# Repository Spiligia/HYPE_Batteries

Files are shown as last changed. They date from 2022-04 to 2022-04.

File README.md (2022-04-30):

**Boston University EC 463 & 464 Senior Design Project**

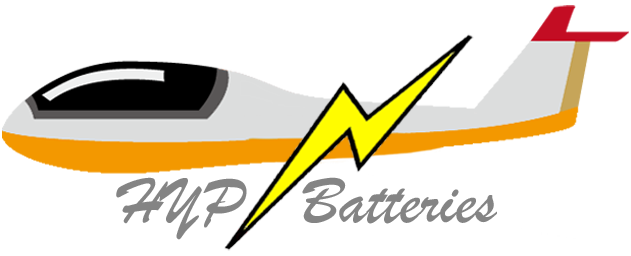
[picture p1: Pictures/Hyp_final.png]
HYP Logo


Members: Spencer Piligian, Ismaeel AlAlawi, Steven Wang, Yusheng Chen and Daniel Kao

## Welcome to Team 23: HYP Batteries! 

Our hybrid-chemistry battery pack design aims to fill niche market gap in high performance battery pack for small aircraft by combining two batteries with two different discharge characteristics. These two cell chemistries can achieve a variable-max discharge rate, allowing us to design a smaller battery pack while also fulfilling power requirements during the launch. This pack setup will help eGliders achieve a safe flight through the use of electric power and as a result, will minimize the risk of mechanical failure for our client’s conventional mechanical engines, whose vibration causes other parts of the aircraft to wear out and ultimately increases the chance of failure.

Link to google drive for more information / process development 

https://drive.google.com/drive/u/0/folders/0AN8LmBJzQ7HJUk9PVA

For member access please email: spiligia@bu.edu

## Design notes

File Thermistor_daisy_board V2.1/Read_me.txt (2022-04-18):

To run these files you will need the latest version of Kicad PCB design software (6.0.x). 
It is free and easily downloadable from https://www.kicad.org/

to open the schematic you will open the temp_proto_v2.1 (KiCad Project 6.0)
to open the pcb file you will open the temp_proto_v2.1 (KiCad Board)

to order a pcb you can either

1. zip this folder and morder from JLCpcb (all 'cam' files in this folder are made w/ respect to jlc's parameters)
2. find the setting in kicad and create new gerbers

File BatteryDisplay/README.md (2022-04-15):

# Battery Display #

App build using Qt Creator

Based on HeatRateGame as a template to check for bluetooth & BLE connection, connect
to devices, discover services and connect to the device to receive BLE data.

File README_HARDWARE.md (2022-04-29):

## Contents
- [Overview](#overview)
- [Battery Temperature Display](#Testbench-Hardware-Setup)
- [Lists of the Hardware Components](#Lists-of-the-Hardware-Components)
- [Setup-Procedure](#Setup-Procedure)
- [3D-Model-Battery-Holders](#3D-Model-Battery-Holders)
- [Ideal Diode](#Ideal-Diode)
- [Temperature-sensing-module](#Temperature-sensing-module)
- [Bill-of-Materials](#Bill-of-Materials)

## Overview

Our project HYP Batteries has several hardware components. These components include designs for a testbench which can handle upto 15A of continuous current, a temperature monitoring circuit schematic for use with a microcontroller, and an Ideal Diode controller for minimization of losses. 

## Testbench-Hardware-Setup

In order to properly conduct this testbench setup, there are several hardware need to be met. On the hardware side, the battery circuit includes a 9V DC power supply that is connected to a 30A relay and that relay is connected to a parallel connection of LiFePO4 and Li-ion batteries in a 3:2 ratio respectively, in which a Schottky barrier diode is placed in series with the Li-ion batteries to prevent reverse leakage current from the LiFePO4 cells to the Li-ion cells.  It is important to note that this Schottky barrier is part of a diode bridge rectifier (i.e. terminals are adjusted accordingly in order to retrieve a single Schottky barrier diode from the rectifier circuit). There exists a 40A fuse that is connected in series with the motor controller and the current sensor for safety standard purposes. In the event of a full short we would expect a current spike up to 550A – ~9.9V/18mΩ (internal resistance) – causing the fuse to blow nearly instantly.  The motor controller is properly connected to an inductor using connection shells and the inductor is then coupled with two power resistors in order to dump energy – by connecting the inductor in series with the power resistor, the current can be tuned easily through the motor controller. For safety reasons, we will be using a thermocouple that will log the temperature of the batteries; the digital thermocouple of the motor controller will log the temperature of the MOSFETs in the motor controller. The battery and motor controller voltages will also be recorded appropriately using multimeters. 

## Lists-of-the-Hardware-Components:
- 3 x LithiumWerks A123 P6 (3.3V, 2500 mAh) lithium iron phosphate (LiFePO4) rechargeable battery cells 
- 2 x Molicel P42A (3.6V, 4200 mAh) lithium-ion (Li-ion) rechargeable battery cells 
- 3 x BeilaMoo 26650 3.7V single slot battery holders
- Surface mount technology (SMT) KeyStone Electronics 21700/20700 dual battery holder w/ coil springs
- IXYS VUO 190-08 NO7 three-phase diode bridge rectifier
- 2 x 1.5kW 1Ω resistors 
- 40A automotive fuse  
- TE Connectivity Potter & Brumfield T9GS1L14-12 30A relay 
- TeamTriforceUK A50S V2.1 (50A burst) VESC-supported motor controller
- XT30 connector (battery input) 
- MR30 connector and cable cover (motor output) 
- 2 x pico-clasp connector shells
- microUSB to USB cable
- 10 µH inductor
- Male-to-male jumper wires
- Test Products Intl. (TPI) dual temperature thermocouple digital thermometer 343
- 1 x 10kΩ resistor
- Alligator clips 
- Crocodile clips
- Hook clips
- Banana plugs
- Electrical ring tongue terminals AWG 18-22
- 2 x TE Connectivity TE2500B1R0J 50 W - 2500 W chassis-mount power resistor 
- AWG 8, 12 & 18 wires
- ACDelco SuperALKALINE 6LR61 9V battery
- PKCELL Extra heavy duty 6F22 9V battery
- 2 x battery snap connectors (9V) 
- Electrical insulation tape and masking tape
- 2 x Multimeter

## Setup-Procedure
- Battery testbench hardware side (see Figure 1 for visual reference)
    - Attach 9V connector battery to the relay (top left and right connections) by soldering battery snap connectors to energize the relay’s coil
    - Place each of the three LiFePO4 batteries in their respective single slot battery holders
    - Place both Li-ion batteries in the dual slot battery holder
    - Solder the wires connecting the LiFePO4 battery holder contacts in series and solder the first ring terminal wire to one of the LiFePO4 battery holders accordingly and the other to the Li-ion dual battery holder to create the parallel connection
    - Connect the ring terminal connected to the LiFePO4 battery holders into terminal ~C (phase-C) of the rectifier and the other terminal (which is connected to Li-ion batteries) to terminal B- (see Figure 2 for rectifier reference schematic) 
    - Solder the LiFePO4 battery holder and rectifier junction into the 30A relay’s bottom right terminal 
    - Solder the 40A fuse into the bottom-right terminal of the Li-ion battery holder and connect its other end to the negative top terminal of the current sensor 
    - Connect the positive top terminal of the current sensor to the motor controller positive XT30 connection; the negative terminal of this connection should be connected to the multimeter accordingly for voltage readings.
    - Connect the positive terminal of the motor controller MR30 connector into the positive terminal of the multimeter to complete the connection for motor controller voltage readings
    - Connect the A50S motor controller to the laptop using micoUSB-USB cable  
    - Connect the positive and negative terminals of the motor controller-motor junction to the positive and negative terminals of the power resistor respectively 
    - The test bench setup should look similar to Figure 3

 - Diode, 9V batteries, and properly soldered electrical connection testing (if necessary)
    - Using a multimeter, test the voltages/currents across the terminals of the Schottky junction diode and the 9V batteries, as well as other electrical connections in the circuit to ensure that the connections aren’t faulty, i.e. improperly soldered or connected.

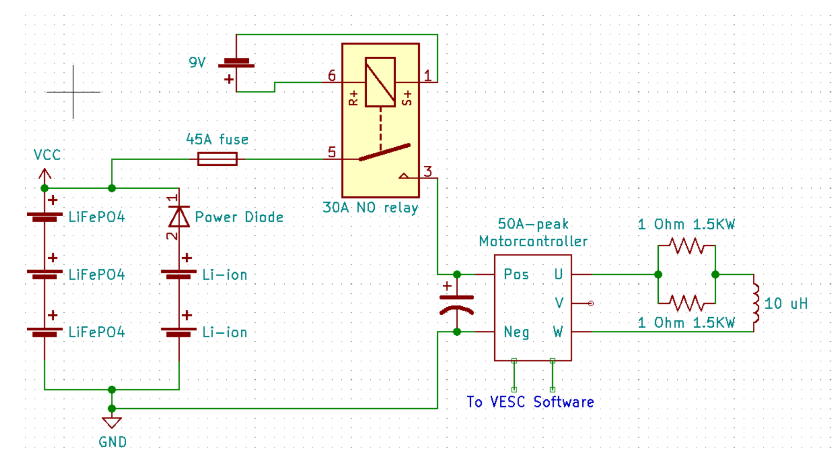
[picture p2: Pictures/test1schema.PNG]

Figure 1: KiCad EDA design schematic of In-lab test 1 (manual current scheduling). Schematic in terms of motor controller design. 

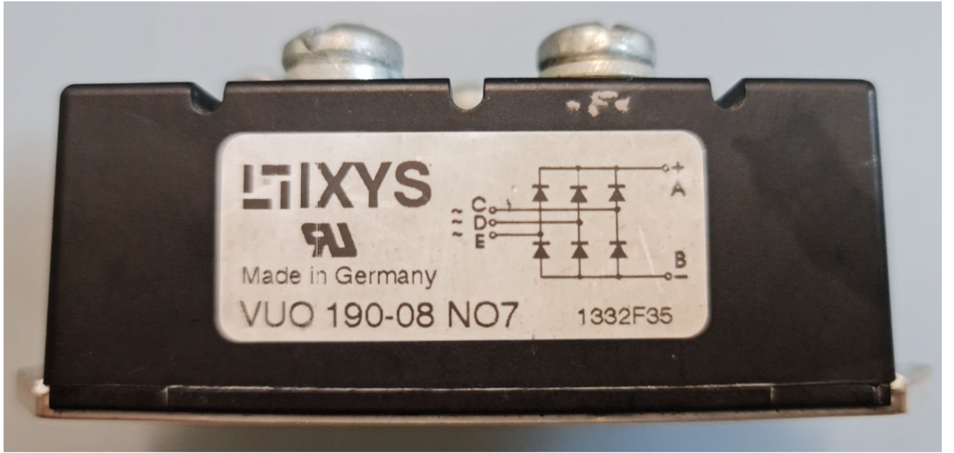
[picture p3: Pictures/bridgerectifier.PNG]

Figure 2: Reference schematic of three-phase diode bridge rectifier. Terminals ~C and B- are used to retrieve a single Schottky barrier from the rectifier. 

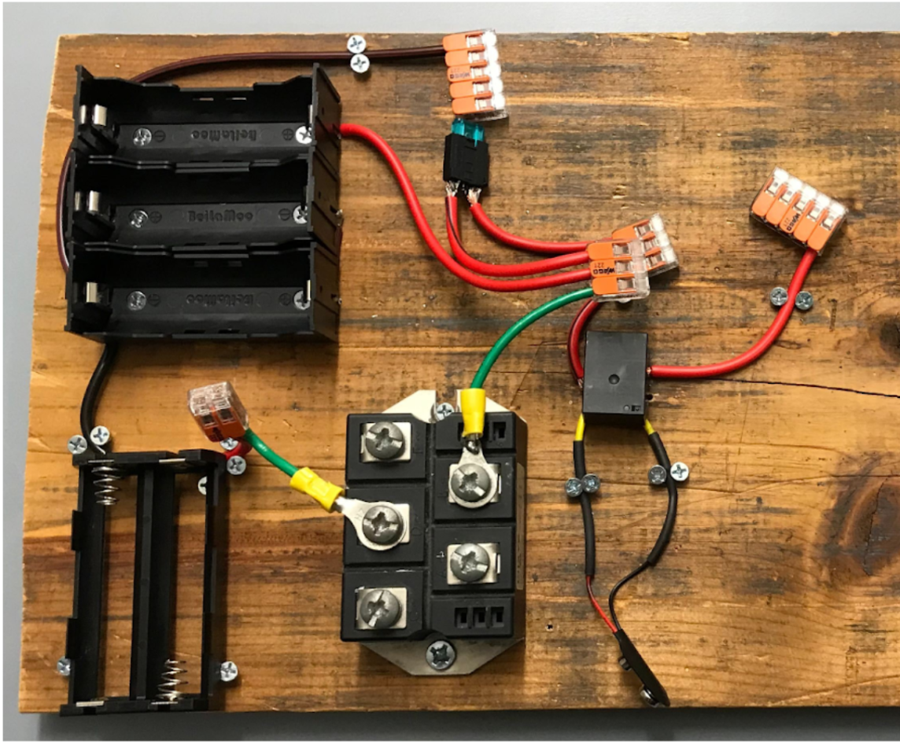
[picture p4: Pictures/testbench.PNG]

Figure 3: Battery testbench reference 

For the future testing,the additional batteries will be added to the testbench when you want to scale up. In additional, you will required to change the fuse and also the wire, since those component are not capable of handling higher current and high voltage. 

## 3D-Model-Battery-Holders
Base on our testing, we found that the battery holder that we bought online are no capable of handling high heat, so we decided to 3D model the battery holders by using pla material. The holder for the LiFePO4 contains the base and the top.(Figure 4&5) For Lithium-ion, it will need two identical 3d models to hold battery in place.(Figure 6) Since our final design pack is 19 series 1 parallel of LiFePO4 and 12 series 8 parallel of Lithium-ion, we will need two sets of LiFePO4 battery holders and 4 sets of Lithium-ion battery holders.  

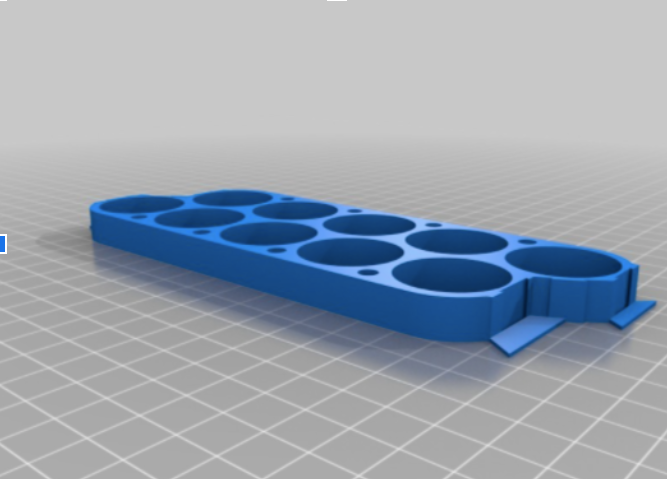
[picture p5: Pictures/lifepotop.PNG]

Figure 4:LiFePO4 Battery Holder Top 26650

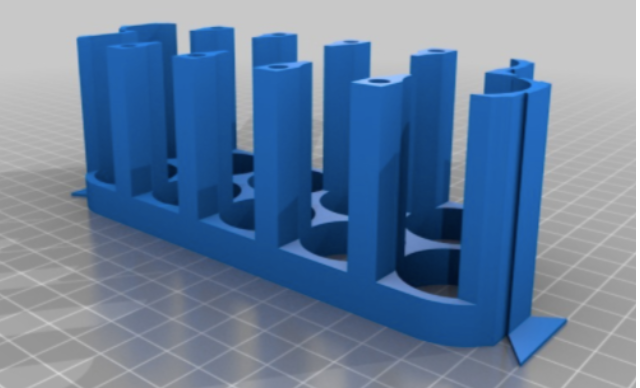
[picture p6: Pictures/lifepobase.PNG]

Figure 5:LiFePO4 Battery Holder Base 26650

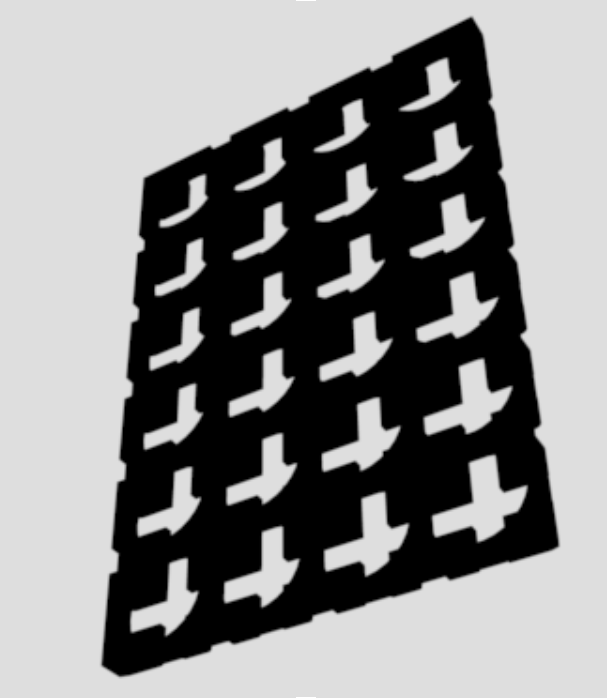
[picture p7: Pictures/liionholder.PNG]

Figure 6:Lithium-Ion Battery Holder 21700

## Ideal-Diode
 
The ideal diode controller will replace the schottky diode for the full scale battery pack. This ideal diode is used to reduce the voltage drop across the diode when the current reaches higher magnitudes. There are two main parts to this component, the ideal diode controller itself and the PCB to house the components. In the PCB, we use two MOSFETs (parts listed in schematic) to distribute the current evenly. To deal with the problem of heat dissipation on the board, we have multiple solutions. The board will have two copper pours on both the top and bottom layers as well as a heat sink on top to further distribute the heat. Additionally, the configuration of the MOSFETs and trace width are also very important for distributing heat. Copper busbars must be soldered on the traces for the 300A current path to help handle the current. More details can be found in the schematics and board diagrams below. 

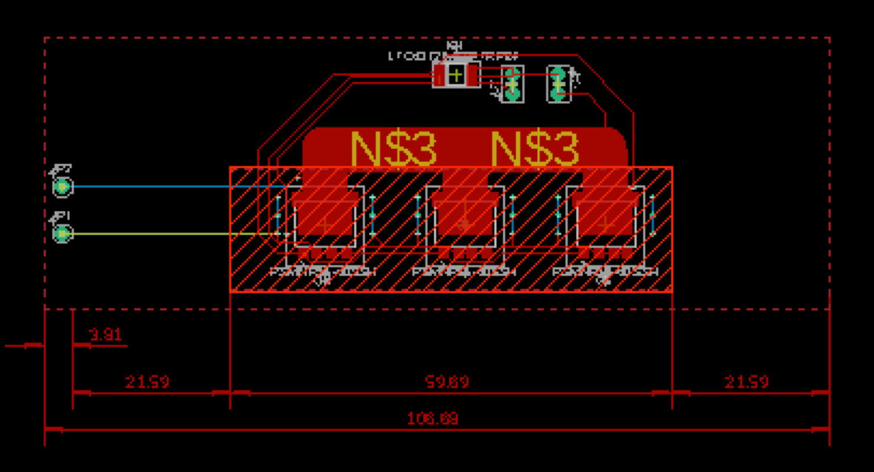
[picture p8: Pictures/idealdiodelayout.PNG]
ideal diode boadr


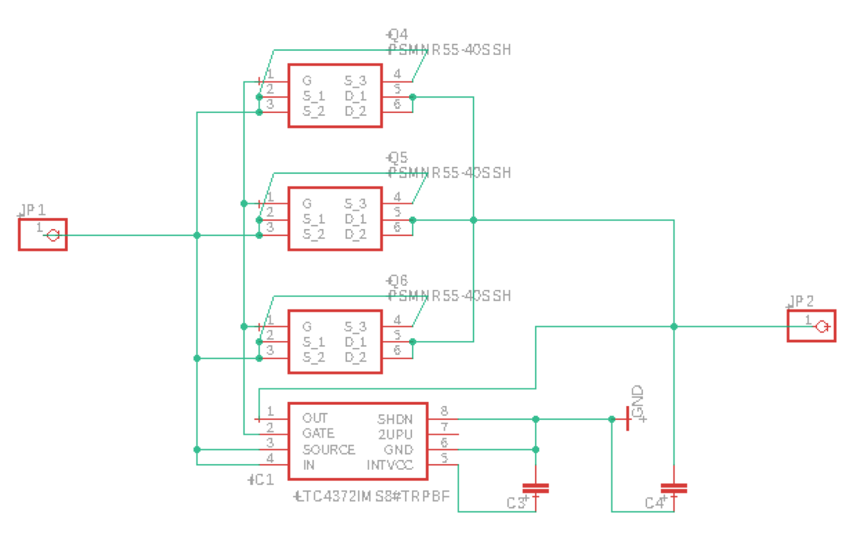
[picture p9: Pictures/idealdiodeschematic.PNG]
idealdiodeschema


## Temperature-sensing-module
The temperature sensing module circuit is based on the use of thermistors in a higher temperature application. Any 10k thermistors will do as long as special care is taken to tuning and programming of the microcontrollers ADC pin and readings. Special care will also need to be taken into account for the speed of the system, specifically rise and fall time. With a 0.1uF capacitor acting as the low pass filter into the final op amp the frequency is limited by the rise time of the capacitor. This can be measured through software simulations or mathematical circuit analysis. To manufacture the PCBs you will need to use KiCAD — a free pcb design software— to get the necessary files to order the PCBs. To set up the modules they will need to be daisy chained in accordance with the circuit diagram to ensure proper orders of signals and functions. A Premade gerber folder is available in Github for the ordering of the boards.

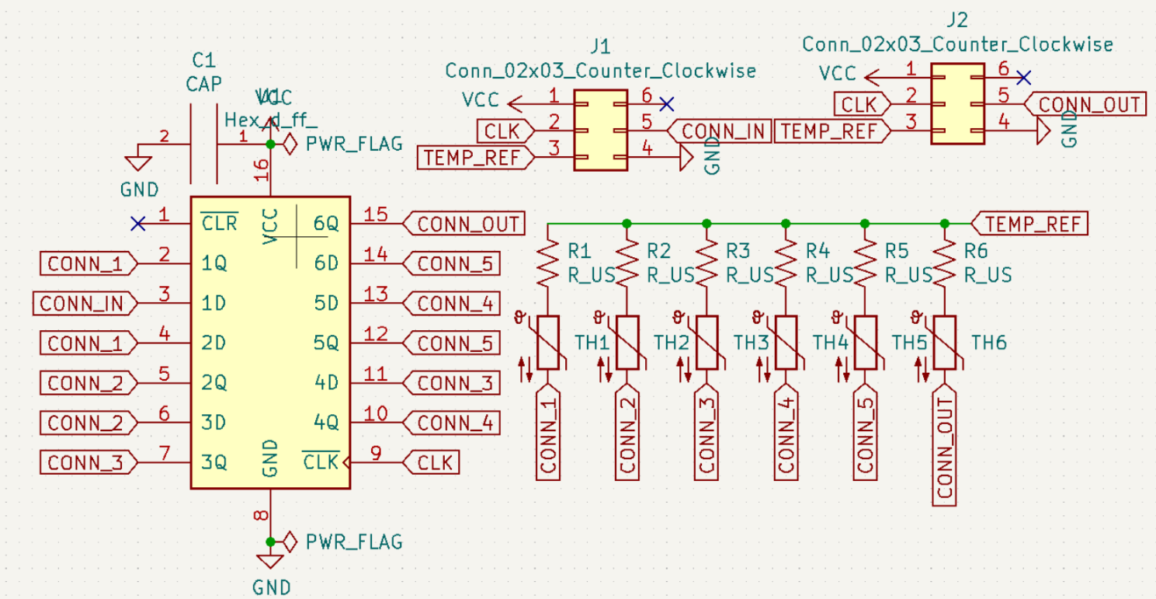
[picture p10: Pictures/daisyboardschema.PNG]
daisyboard1


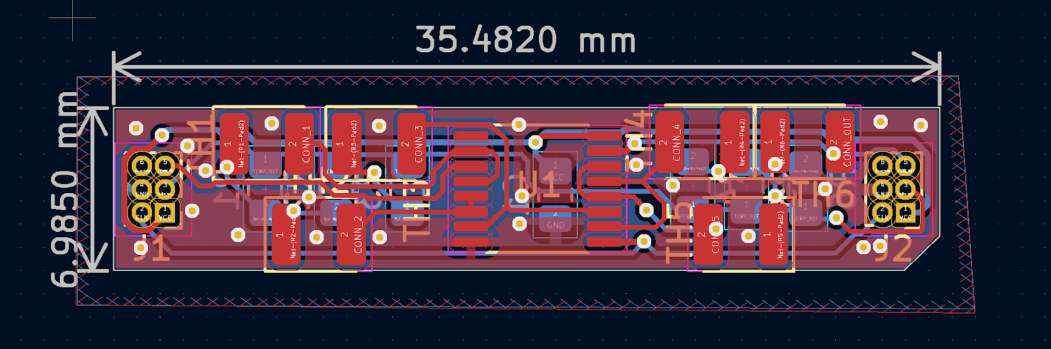
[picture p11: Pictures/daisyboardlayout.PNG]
daisyboard2


## Bill-of-Materials

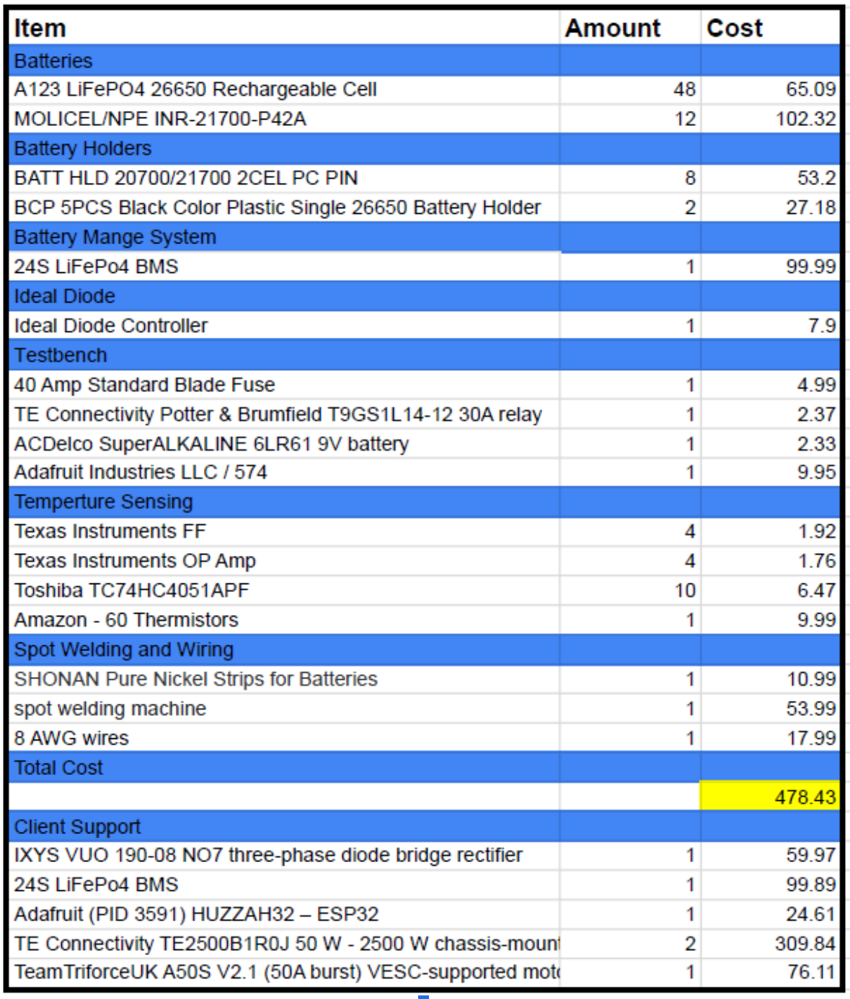
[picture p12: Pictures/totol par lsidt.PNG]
bom


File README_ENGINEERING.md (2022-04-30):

To quick start this project first read throught the software and hardware README reports. The project can be split into three sections: Battery, Hardware and Software

## Battery-Pack
If you like to come up with your own configuration of the battery pack, you can use the simulation code provide in the Simulation_Code_and_Result folder. The spec sheet of different batteries are in the folder called Battery_Pack_Design, this will help you to create csv file for the simulation code. The process of creating csv file are listed in the software README_SOFTWARE.md. You would be able to come up different graphs and charts showing details such as power, discharge rate, voltage and etc. 

## Hardware 
One may want to test on the pre designed testbech and the schematic provided in the hardware README will allow for easy hardware setup. The README_HARDWARE.md provide the process of the testing and also the materials been used for testing. 

To start this project one would want to produce and test the ideal diode design and the temperature sensing module. The next step is to take the information gained from that and iterate the designs. Then combine the temperature sensor data with the battery temp viewer to finalize the system for the client. 

If someone want to looks at past prototype results and also self test results and it is in the folder called Prototype_Test and Self_Test. 

It is possible to increase the voltage and currents to the full battery size and then design mechanical components to ensure isolation from the cabin and safety from factors like vibration and drops. Since our model is just an small scale model of the whole pack, scaling up the battery pack may increase the safety concern.

## Software

If changes and revision need to be done to the simulation or battery display see README_SOFTWARE.md for more information regarding setting up the proper simulation tools and source code for the project.

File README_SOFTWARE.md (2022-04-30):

Team #23 Software Report

## Contents
- [Overview](#overview)
- [Battery Temperature Display](#Battery-Temperature-Display)
- [Qt Creator Download Instruction](#Qt-Creator-Download-Instructions)
- [Qt Creator Interface](#Qt-Creator-Interface)
- [Instruction to run Battery Display App](#Instruction-to-run-Battery-Display-Application)
- [Battery Temperature Simulation App](#Battery-Temperature-App)
- [Battery Pack Configuration Simulation](#Battery-Pack-Configuration-Simulation)
- [Battery Pack “Naive” Testbench Automation](#Battery-Pack-“Naive”-Testbench-Automation)
- [Battery Pack Structural Testbench Automation](#Battery-Pack-Structural-Testbench-Automation)

## Overview

Our project HYP Batteries has three software operations required to test our hardware: battery pack simulation, battery pack temperature monitoring, and battery pack automated testing. 

## Battery-Temperature-Display

The preferred integrated development environment (IDE) for battery temperature display is Qt Creator which is a cross platform for C++, javascript and QML. The software is available to download online through Qt Creator website, https://www.qt.io/.

## Qt-Creator-Download-Instructions

1. Users must click on the download button below the website
2. Direct to “Downloads for open source users” to get a free copy
3. After navigating to that page the user will need to scroll all the way down 
4. Then hit the download button and follow along with the instructions. You might need to download additional features like Xcode & Xcode command line tools for Mac OS
5. Select an installation folder on your device and check off custom installation
6. Under custom installation page select Qt 6.3.0 default feature which will selection all options within the folder
7. Afterward read Terms of Service page and begin downloading process for Qt Creator

## Qt-Creator-Interface

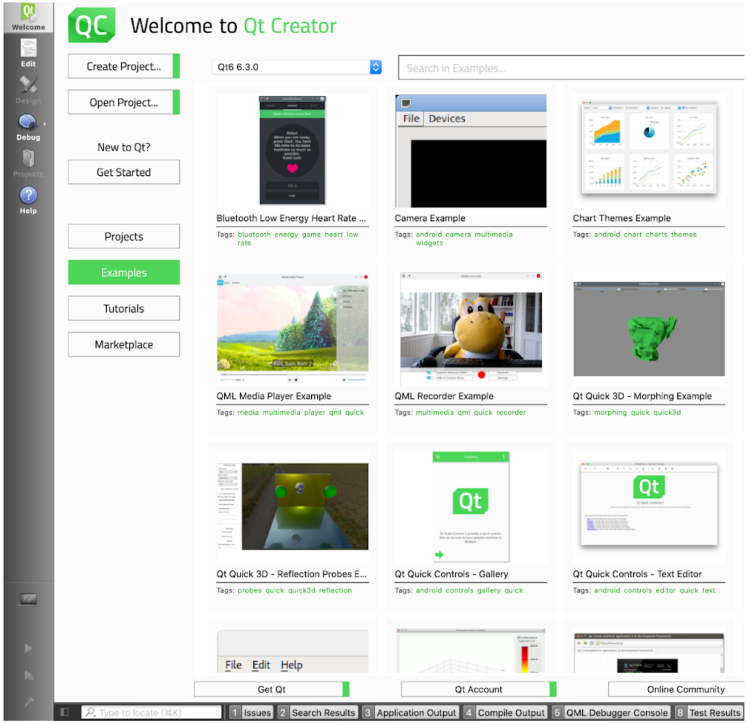
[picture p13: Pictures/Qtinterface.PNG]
qt interface pic


Basic rundown of Qt creator interface, welcome tab is where you can find example templates, create and open projects, the edit tab will be the project you're working on after you select a file on the welcome tab, the computer icon is how you wish to emulate the app, there’s two play button one to run the file and other is to debug, lastly the hammer icon is to compile the files prior to running.

## Instruction-to-run-Battery-Display-Application

After downloading Qt Creator navigate to github to download the source code for battery temperature display app: https://github.com/Spiligia/HYPE_Batteries/tree/main/BatteryDisplay. From there launch the Qt Creator application and open the project, make sure you select the Battery Display folder. Navigate to the Measure.qml file to adjust the amount of battery cells you desire in series and parallel. From there you can choose to emulate the application on the PC or another platform either Android or Apple. You must have additional packages downloaded to run on either Android and Apple platform that Qt Creator would recommend to download prior to building the files.  

## Battery-Temperature-App 

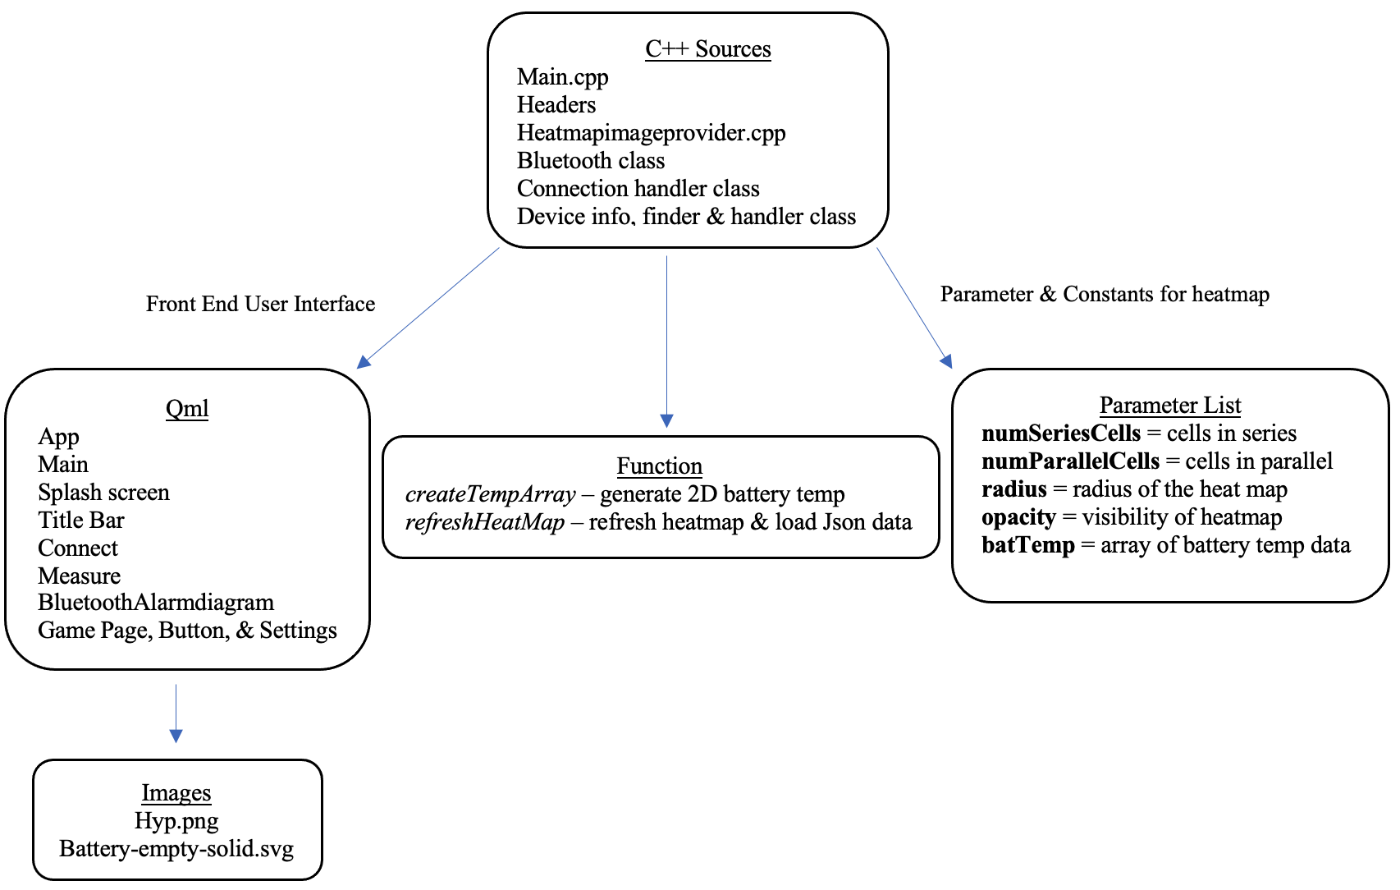
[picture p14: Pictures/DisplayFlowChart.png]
Display FlowChart


The battery temperature display used Qt Example: Bluetooth Low Energy Heart Game as a template for its design that can be found under the Examples tab on Qt Creator. The C++ Sources are mainly untouched except for Heatmapimageprovider.cpp, this was sourced from our client. The following QML files were modified to accommodate the app design: SplashScreen.qml, TitleBar.qml and Measure.qml. Below are relevant documentations done to the user interface in the qml files and the cpp file: 

- SplashScreen.qml: added logo image for the app
- TitleBar.qml: changed the page indicator size & text on the app title navigation bar
- Measure.qml: comment out unused code from the heart rate game, added heatmap image & integrate parameters required for it to function from Heatmapimageprovider.cpp, added command to display & remove heatmap temperature data on UI & User console, function to generate random heatmap data temperature and reload heatmap button
- Heatmapimageprovider.cpp: added new Json Array object batTemp to grab random generate temperature data and attempt to write onto the actual heatmap on the UI
	
## Battery-Pack-Configuration-Simulation

In order to do the simulation, a notebook environment that can write and read Julia script is needed. After obtaining a coding environment like Jupyter notebook, the next steps are to obtain battery data specification sheets for the batteries you wish to simulate. These specification sheets must include: cell capacity, cell voltage, charge current, discharge current, weight, and discharge rate characteristics. The discharge rate characteristics need the voltage versus capacity relationship curves for different discharge rates. The discharge rate characteristics will help approximate the voltage versus capacity relationship curve for our desired discharge rate. Additionally, information about the aircraft being simulated will be needed, specifically: airplane mass, climb velocity, and glide ratio. These specifications will be used to determine the height of the aircraft during flight. Lastly, a diode will be needed in the circuit to prevent leakage current in the lithium-ion battery. This simulation will account for this, but value for diode voltage drop is required. 

We will need to create CSV files for simulating the configuration of the battery pack. Based on the spec sheet giving from the manufacturer, we will need to input 60 to 70 data points of battery capacity (Ah) with the corresponding voltage (V) for a specific discharge rate. Moreover, we will need at least 3 to 5 different discharge rate for the code to work.

The file is called hybrid_battery_analysis_final.py in the github resources. Here are the steps for this code.

1. Download Anaconda Navigator from the internet and install the jupyter notebook 6.3.0
2. Upload the code to the jupyter notebook
3. Download Julia 1.6.3 from the internet 
4. Install Plots, CSV, DataFrames, and Interpolations packages into Julia environment
5. For each lithium ion battery type desired specification for testing
    - Import discharge rate CSV files
    - Input single cell capacity, single cell mass,single cell maximum discharge rate,and individual cell energy capacity from the spec sheet provide by the manufacturer 
6. User Tunable Parameter Section
    - Choose which lithium ion battery pack to test
    - The first line specifies the pack being tested
        - Set “pack = [ lithium ion battery being tested ]” 
    - Input number of series rows & parallel columns under the “if statement” for specified lithium ion battery
    -  Input number of series rows & parallel columns under the “if statement” for specified LiFePO4 battery
7. Input Aircraft Data 
    - Set “airplaneMass = [ mass in kg ]”
    - Set “climbVelocity = [ velocity in m/s ]“
    - Set “glideRatio = [ glide ratio of aircraft ]“
8. Diode
    - Set “v_drop_diode = [ voltage drop in V ]”
9. Stimulation Parameters
    - Test and change configuration of series and parallel lithium ion and LiFePO4 battery pack to achieve desired height and weight

The code will automatically create graphs and charts for the user to have a better understanding on each configuration. Through the graphs and charts, users will be able to adjust the number of the battery cells they are using and also adjust the type of the battery cells in the battery pack.  

## Battery-Pack-“Naive”-Testbench-Automation
The following software packages are needed before proceeding with the software configuration instructions:

- VESC Tool (free version) GUI developed by Benjamin Vedder
    - Qt Toolkit
    - .zip file extractor (Windows, Linux, Mac OS X, and Android supported like WinZip or 7-Zip)
     - Source code: https://github.com/vedderb/vesc_tool
 - VESC-Lisp, Common Lisp, or LispBM Scripts
     - ANSI Common Lisp GNU v2.49 (2010-07-07 build) compiler (REPL)
     - For Mac OS X, install via MacPorts 
     - For Windows and Linux (Ubuntu, Debian, Sun Solaris, etc.), install directly from https://clisp.sourceforge.io/

To setup the VESC Tool, follow these instructions: 

 - Create an account on https://vesc-project.com/ > click on “VESC tool’ tab > purchase VESC Tool Free for €0.00 (no billing information required) > click on “Purchased Files” link (top right corner) > download and extract “vesc_tool_BETA_ALL.zip” (or for Windows users, download “vesc_tool_free_windows.zip”)

 - Alternatively install directly via source code: https://github.com/vedderb/vesc_tool

 - For Windows and Linux users, Install REPL Lisp compiler via SourceForge 

 - For Mac OS X users install MacPorts v2.7.1
    - Install Xcode and Xcode Command Line Tools
Agree to Xcode license in Terminal: sudo xcodebuild -license
    -  Install MacPorts according to version of  OS X (convenient installation through .pkg installer for version 10.15+) on https://www.macports.org/install.php
    - After MacPorts installation, type sudo port install clisp to install common lisp implementation (interpreter, compiler, debugger, etc.)

After having performed extensive manual testing of the hybrid battery pack, the team later on started researching a more modular, automated means of testing the pack, in which they stumbled upon Lisp. Lisp (List Programming) is the second oldest high-level programming language (developed in 1958 by John McCarthy at MIT) that is built from s-expressions, which are essentially lists (or sequences of atoms, i.e. numbers, contiguous characters, and strings) that are enclosed in parentheses. This was particularly suitable for AI programs at the time as the arguments that are passed to the REPL (Read-Evaluate-Print-Loop) interpreter are very efficiently processed (i.e. efficient processing of symbolic information). From our research, Common Lisp was primarily used from 1980 to 1990, and is the dialect that we started learning accordingly. However, over the past decades, Common Lisp has branched out into so many different dialects like ArcLisp, HyLisp, NuLisp, Liskell, and so on, as well as the more recently developed dialects like Bel developed by Paul Graham. In fact, AutoCad was built in the Lisp language, and has its own dialect called AutoLisp! So, it is not unreasonable to say that this scripting language is still a very rigid choice today given its high symbolic processing efficiency.

Thus, it is not surprising to find that Lisp is used in a myriad of embedded system development applications, where both conciceness of code, CPU & memory usage, and embedded system performance & efficiency are crucial factors. Lisp provides very powerful macro definition machinery as well and the more recent dialects mandate garbage collection, which is a very attractive feature; notwithstanding, its REPL provides user-friendly and interactive programming for embedded systems. In the case of 32-bit ARM microcontroller units (MCUs) like STM32 or NRF52, Lisp Black Magic (LispBM) is a wisely used dialect of Lisp which is implemented in C and can be "embedded" into some application running the given MCU to make the application scriptable using a lisp-like syntax. This version of Lisp was developed by Joel Svensson who is a researcher at Chalmers University of Technology within the area of functional programming. He was inspired to add this dialect to the family of MCU-lisps after taking MIT's 6.001 Structure and Interpretation of Computer Programs series of lectures. We’ve been in constant communication with him on Discord and he's been guiding us through the language and providing us with relevant learning resources for reference, as well as extensive documentation on his Github page. He had pointed out to us that learning Common Lisp is somewhat different from learning MCU-lisps like LispBM, and so shifting our focus to learn LispBM instead for the purposes of MCU embedded development. 

The VESC-tool developed by Benjamin Vedder allows for an interactive means of testing our battery pack. In particular, it allows us to have a lot of freedom in both tuning, tracking, and analyzing many of the parameters involved in the process of scaling up the pack like the battery temperature, MOSFET temperature, motor current and voltage, duty cycles, power levels, power level transitions, etc. So as to make the project more straightforward and understandable, the first step of testbench automation can be naive. That is to say, users can open the file naive_testbench.lisp in order to automate a “naive” automation of the motor current (using the set-current function) while previewing the real-time series plots on the VESC tool.

## Battery-Pack-Structural-Testbench-Automation
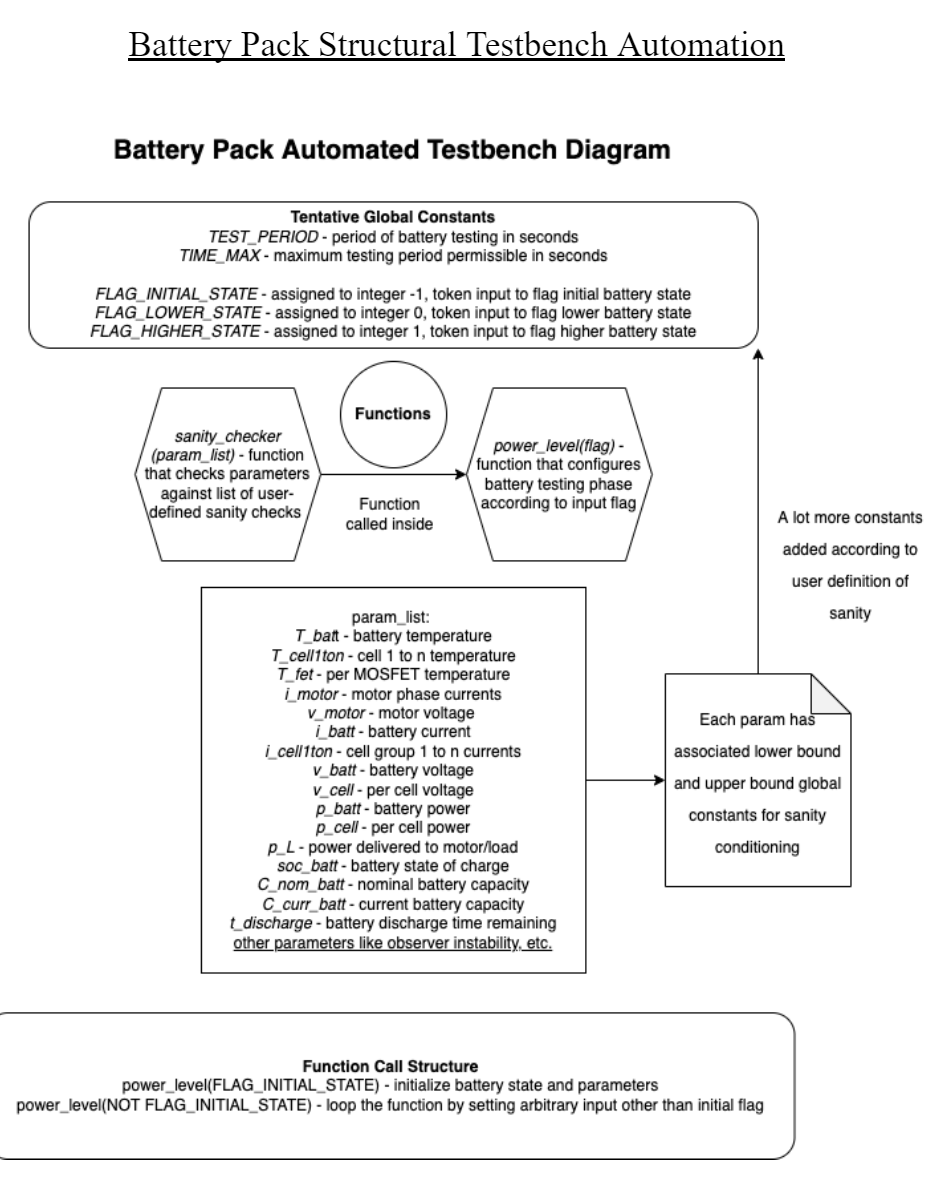
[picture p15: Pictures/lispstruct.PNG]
lispstruct
 
The testbench code found in battery_testbench_v1.00.lisp should have some loop with at least four “top-view” conditions (a.k.a. battery monitoring sanity checks) and then it should have some actuation mechanism where as long as those conditions are satisfied, then the next phase of testing will begin according to the state variable or parameter list. So, the top view diagram provided above lists the definitions and relations between the following relevant battery testing parameters:

 - t_test - Testing period (time set for testing that is measured in seconds and ranges from 0 to TIME_MAX), where TIME_MAX is some constant that is defined by the user or client accordingly
 - user_stop - User-defined input (manual STOP command of testing)
 - sane & insane - Sane state is that which meets the conditions involving each parameter outlined below, and insane is that which doesn't otherwise 
     - T_batt (battery pack temperature, however it is defined), T_cell1, T_cell2,..., T_celln (temperature of each cell as defined by the engineers)
    - T_fet (MCU MOSFET temperature)
    - i_motor (motor phase currents)
    - v_motor (motor voltage)
    - i_batt (battery current), i_cell1, ... , i_celln (given cell group current)
    - v_batt (battery voltage) and v_cell (per cell voltage)
    - p_batt (battery power), p_cell (per cell power), p_L (current power delivered to load/motor)
    - SOC_batt (battery state of charge)
    - C_nom_batt (nominal capacity of battery), C_current (current capacity of battery)
    - t_discharge (time remaining for battery to discharge)

As for the functions used in the diagram: 

- power_level(flag) - A power level function that sets relevant parameters according to some input token (“flag”)
    - the power level function determines the initial state of the battery and sets the relevant parameters (initial values)
    - the input token determines whether or not the test transitions to a higher or lower power level or shuts down
    - the function prints relevant parameters to the console for debugging and even manipulate some data if needed
- sanity_checker(param_list) - A sanity check function that evaluates the current battery state and set its values according to a number of conditions
    - the sanity checks are conditions that are defined such that some flag token is set to some value corresponding to sane or insane
    - either power level function is called in the sanity check function (or vice-versa possible) to parse the sane/insane flag inputs and transition the power level according to that flag token. If the flag input is sane, then power is transitioned to higher level, and otherwise, if it's insane, then the power is transitioned to lower level
    - in the definition of the sanity check function, the function itself is called again in order for it to loop indefinitely according to some sleep frequency (similar to void loop in Arduino IDE)

After defining the power level function and sanity check function in the lisp script, the power level function would be first called with the corresponding input token for initializing the battery state and determining its relevant parameters (i.e. it runs once similar to void setup in Arduino IDE). Then, the sanity check function would be directly called with the outputs of the power level function as its inputs.

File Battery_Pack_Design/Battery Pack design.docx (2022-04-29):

Li-ion (only search in stock 18650 battery shop)-benchmarking and search

Samsung 25R 18650 2500mAh 20A Battery:

Store link: https://www.18650batterystore.com/products/samsung-25r-18650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

Datasheet:

https://cdn.shopify.com/s/files/1/0481/9678/0183/files/samsung_25r_data_sheet.pdf?v=1605015771

14s12p for 58.8V and 30Ah a total of 168cells @ 5.25/cell (100+order) = $882(Expensive)

Notes: Pack is perfect for our purposes but expensive

# Molicel P26A 18650 2600mAh 25A Battery:

Store link:
https://www.18650batterystore.com/collections/18650-batteries/products/molicel-p26a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

Datasheet:

https://cdn.shopify.com/s/files/1/0481/9678/0183/files/molicel_p26a.pdf?v=1605879122

14s12p for 58.8V and 31.2Ah a total of 168cells @ 3.55/cell (100+order) = $596(Expensive)

Notes: Pack is perfect for our purposes but expensive-less so than samsung

For Li-ion(14sNp)

It is now I realize to make this pack we will need MOH POWEH so to do this we will use cells that can handle a TON of current so I will be pursuing this avenue from here on out, the launch is only ~3 mins for pack 1 and 7 for pack 2 so hopefully we can beat these batteries up a little bit for the weight savings

# Molicel 21700 P42A 4200mAh 45A Battery:

Store link:
https://www.18650batterystore.com/products/molicel-p42a?_pos=1&_sid=ff008a6b1&_ss=r

Datasheet:

https://www.imrbatteries.com/content/molicel_p42a.pdf

Two configurations possible:

1. Power Delivery

14s5p for 58.8V and 21Ah a total of 70cells @ 4.94/cell (50+order) = $345.80 Least expensive so far

2. Power and Energy Delivery

14s7p for 58.8V and 29.5Ah a total of 98+2(savings on bulk)cells @ 4.84/cell (100+order) = $474.32(Expensive)

Notes: can we cut the total energy of the pack by ⅓ ?

# LiFePO4

IMPORTSNT NOTE: Will only need 100s of operation out of this pack , we can push the batteries hard.

# ANR26650M1-B, LithiumWerks Nanophosphate® 3.3V 2.5Ah Lithium Iron Phosphate Battery

Store link:
https://a123batteries.com/anr26650m1-b-lithiumwerks-nanophosphate-3-3v-2-5ah-lithium-iron-phosphate-battery/

Datasheet:

https://a123batteries.com/product_images/uploaded_images/26650.pdf

17s4p for 61.2V and 10Ah a total of 68cells @ 6.00/cell (29+order) = $408

420A for 10s at 48C rate or 200A continuous at 20C rate

Notes: Using matlab plot 300A would be about 27C rate, probably handleable for 60s will need to test.

(for testing 21s2p)-for LiFePO4

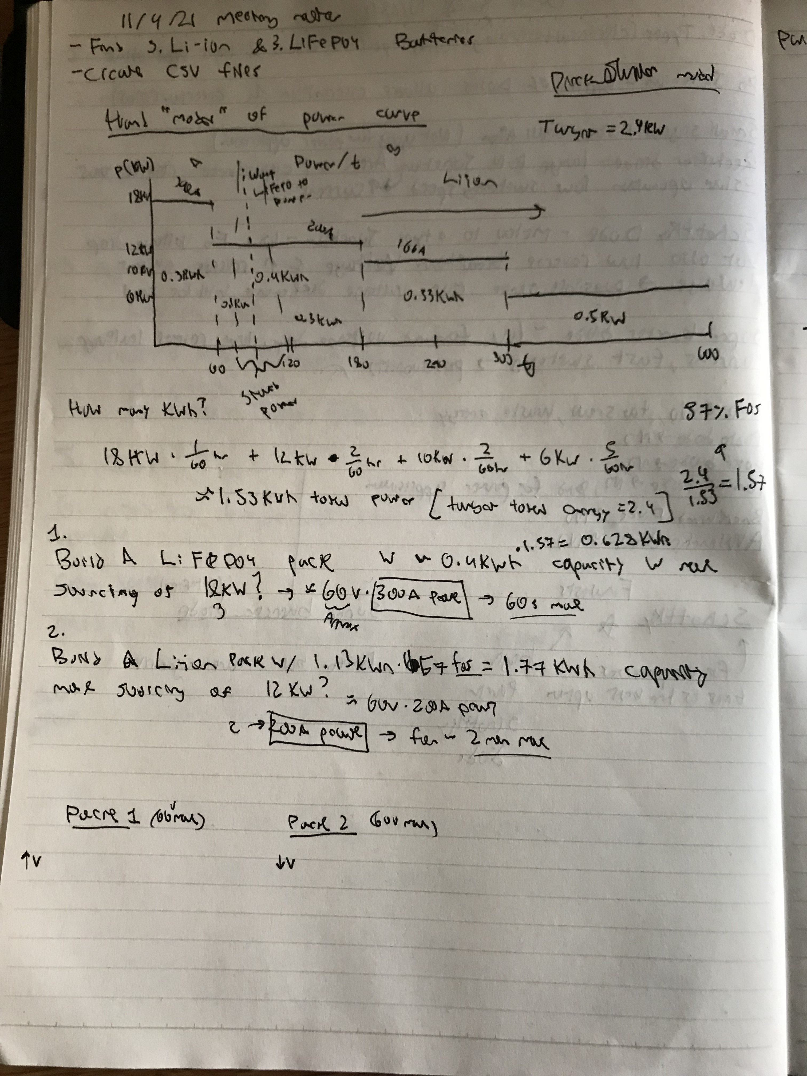
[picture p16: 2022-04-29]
Battery_Pack_Design/Assumptions.jpg

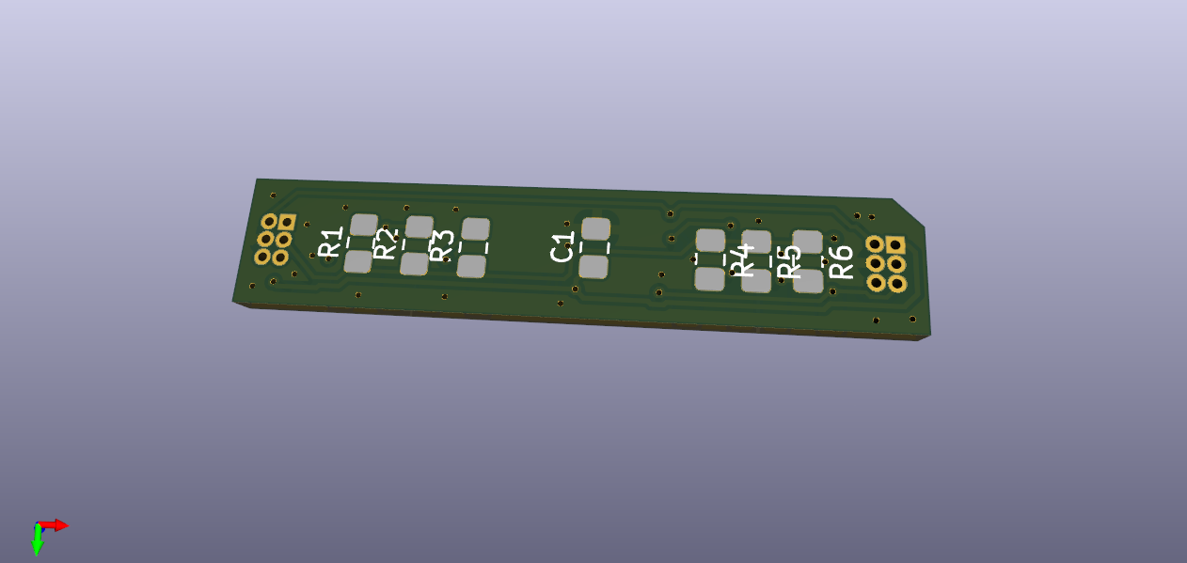
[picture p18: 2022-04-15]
Thermistor_daisy_board_v3_render_back.png

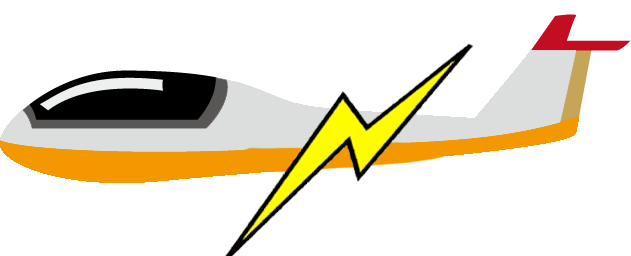
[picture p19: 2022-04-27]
Pictures/HypBat1.png

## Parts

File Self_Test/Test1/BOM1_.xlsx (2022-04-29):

Materials: | Units | Price: | Use: | links:
Switch | 1 | 0.4 | handle at least 2A
Breadboard | 1(small) | On hand (2) | handle at least 2A
Battery: LiFePO4 | 3 | on hand
Battery: LI-ion | 3 | 2 on hand
Wires | N | Pho 105 (lab + Senior Design lab) | Handle at least 2A
nickle plate | N |  |  |  | 10V*1 = 10W
Battery holder LI-ion | 3 | 3D Print
Battery holder LiFePO4 | 3 | 3D Print
Terminals: Connectors | 2022-04-12 | TBA | Handle 5A
Resistor 10ohm 20-25W | 1 | $7 - 10 | handle max amp for long time
Have testbench: |  | In Lab
Multimeter

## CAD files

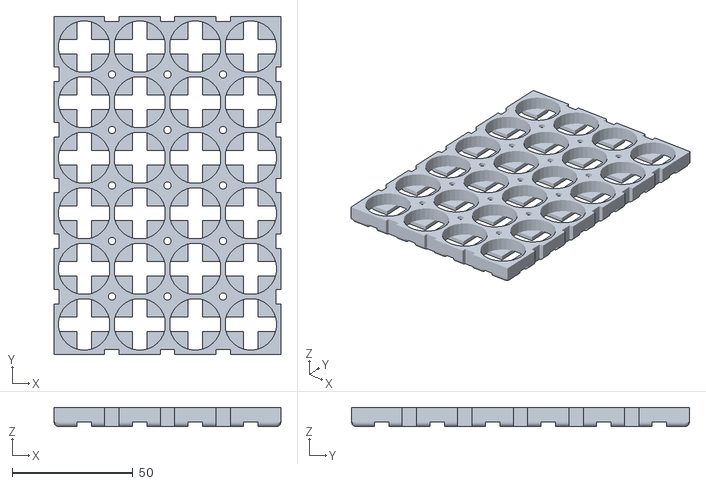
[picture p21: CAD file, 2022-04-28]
3D_Battery_holders/battery-holder_20191218-62-1btny9i.stl
94.0 x 140.0 x 7.99

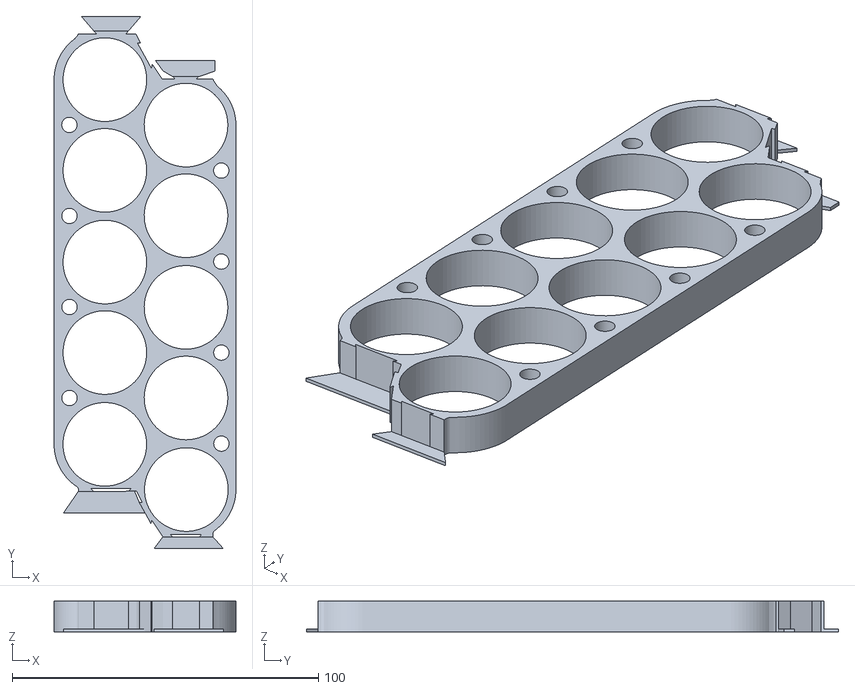
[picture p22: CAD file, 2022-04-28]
3D_Battery_holders/Soporte_baterías_26650x10_base_superior.stl
59.4 x 173.7 x 10.0

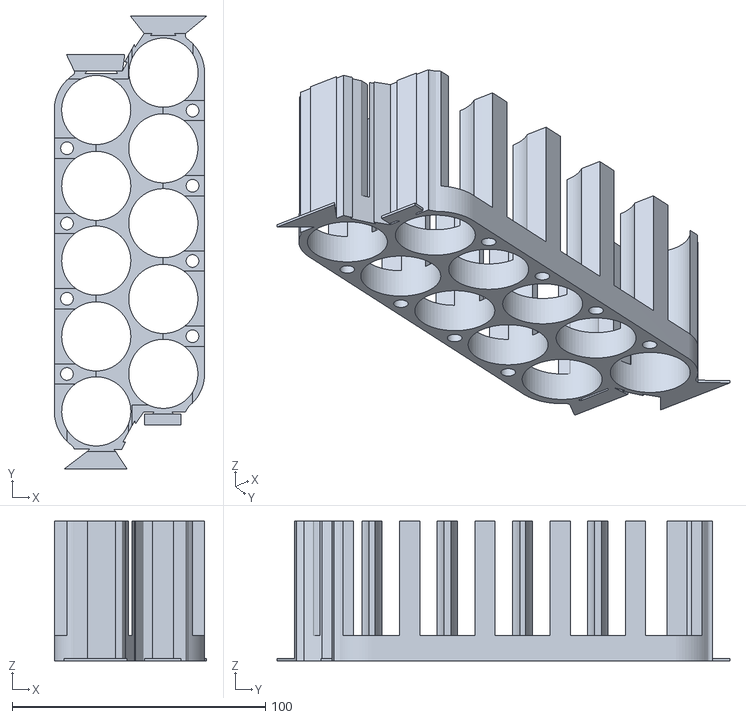
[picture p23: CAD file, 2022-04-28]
3D_Battery_holders/Soporte_baterías_26650x10_base_inferior.stl
60.2 x 178.9 x 55.2

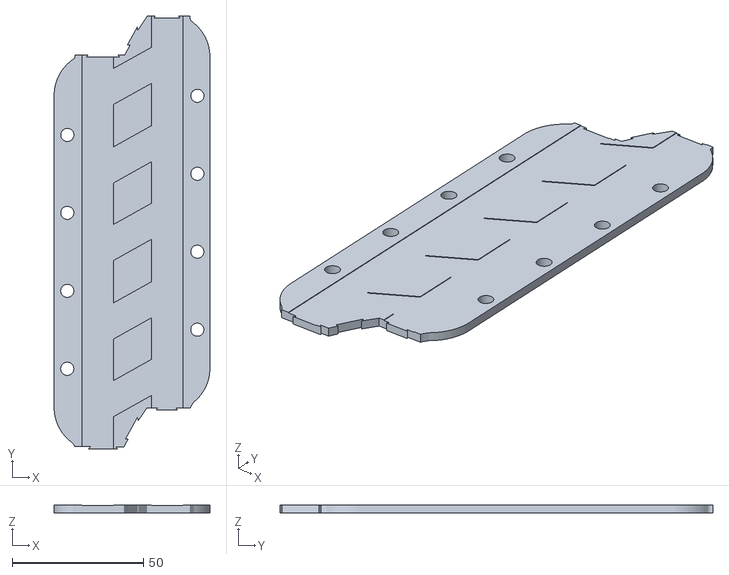
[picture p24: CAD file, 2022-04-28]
3D_Battery_holders/Soporte_tapa_derecha.stl
59.4 x 165.0 x 2.90

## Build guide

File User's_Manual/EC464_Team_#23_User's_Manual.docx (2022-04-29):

# Boston University

# Electrical & Computer Engineering

# EC464 Capstone Senior Design Project

# User's Manual

Hybrid Battery Pack for Self-Launching eGliders

Submitted to

CyPi Ltd.

Dr. Kenneth D. Sebesta

859-648-0272

kenn@cypiltd.com

by

Team #23

HYP Batteries

Team Members

Spencer P. Piligian, spiligia@bu.edu

Daniel Kao, dkao1234@bu.edu

Yusheng Chen, chenyush@bu.edu

Steven Wang, swang3@bu.edu

Ismaeel AlAlawi, ialalawi@bu.edu

Submitted: April 18, 2022

Hybrid Battery Pack for Self-Launching eGliders

#### Table of Contents

Executive Summary iii

1 Introduction 1

2 System Overview and Installation 3

2.1 Overview block diagram and software architecture 3

2.2 User interface 6

2.3 Physical description 6

2.4 Installation, setup, and support 6

3 Operation of the Project 11

3.1 Operating Mode I: Normal Operation 11

3.2 Operating Mode II: Abnormal Operation 11

3.3 Safety Issues 11

4 Technical Background 13

5 Relevant Engineering Standards 16

6 Cost Breakdown 18

7 Appendices 20

7.1 Appendix A - Specifications 20

7.2 Appendix B – Team Information 22

# Executive Statement

Batteries for eGliders are a niche market, because they demand performance similar to that required for a rocket launch while still needing to be lightweight enough for a small aircraft. As a result, there are currently no cheap commercial off-the-shelf battery packs suitable for an eGlider. Our hybrid-chemistry battery pack design aims to fill this gap by combining two batteries with two different discharge characteristics. These two cell chemistries can achieve a variable-max discharge rate, allowing us to design a smaller battery pack while also fulfilling power requirements during the launch. This pack setup will help eGliders achieve a safe flight through the use of electric power and as a result, will minimize the risk of mechanical failure for our client’s conventional mechanical engines, whose vibration causes other parts of the aircraft to wear out and ultimately increases the chance of failure.

# 1 Introduction

An eGlider's self-launch profile is much like that of a rocket’s: both require a period of high thrust followed by discrete reductions in power output.

1. Peak-power ground acceleration (0m/s -> 25m/s)

2. Peak-power climb to Safe Altitude (0m -> 100m)

3. Max continuous-power climb to Airport Pattern Altitude (100m- > 300m)

4. Gentle climb to Thermal Altitude (300m -> 500m)

5. Level flight at Thermal Altitude (500m)

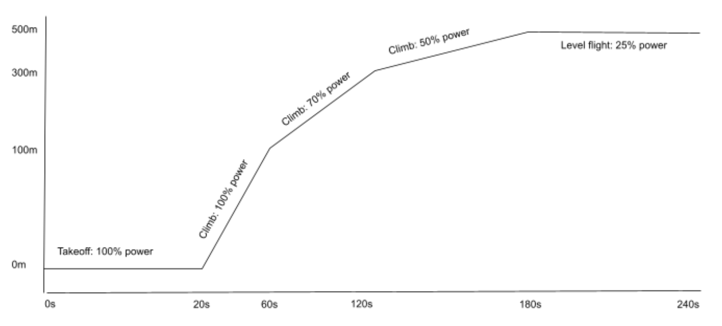
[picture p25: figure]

Figure 1: Self-launch profile of an eGlider.

This self-launch lasts approximately four minutes. Based on the launched profile prediction we made, we can estimate the power use at different stage launching. Ideally, the battery pack will use all its energy by the end of the launch. Reaching the desired altitude with more energy capacity than is necessary maximizes weight, cost, and fire risk – all of which are undesirable traits in aviation.

Current battery technology does not allow for a small, safe battery pack capable of meeting the rocket-launch requirement: lithium iron phosphate (LFP) batteries are too fire prone, and individual lithium-ion (Li-ion) batteries do not have the ability to source the intense currents required for launch on their own.

The current solution is to install a battery pack which is much larger than ideal. This larger pack allows Li-ion cells to share the current load, bringing the per-cell current to a survivable 2-4C discharge rate. However, the downside is a pack which only uses 20% of its capacity for launching, which means the pack is 70-80% heavier than optimal.

A hybrid LFP / Li-ion pouch cell pack delivers a blend of power and energy. The LFP is capable of sourcing more than 100A for short bursts, though it does not have great energy density. The Li-ion pouch cell has great energy density, but cannot source more than 30A per cell.

In a cell series count ratio of 3:2, simulations show that the desired power properties are evident, and the proposed pack weighs two to three times less than the current state-of-the-art.

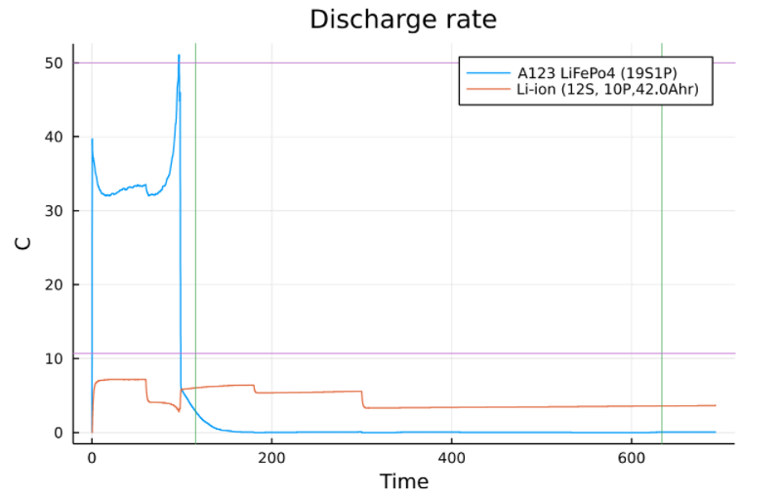
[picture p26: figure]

Figure 2: Julia software simulation.

Please carefully read and follow the instructions to ensure the safe use of our battery pack. Since the battery pack can go over 60V and capable of discharging at 300A, failure to follow the instruction may cause injury and cause damage to the battery pack.

The following sections will provide deeper descriptions on the system and give instructions on how to operate the battery pack appropriately.

# 2 System Overview and Installation

## 2.1 (a) Overview block diagram

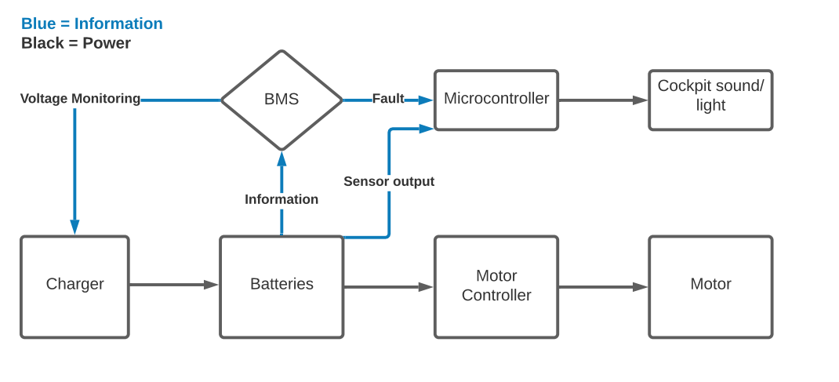
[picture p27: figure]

Figure 3: System overview block diagram with labeled functional and information flow lines.

As per the figure above, the block functions of the battery pack are split into two main categories: information and power. While the batteries are being charged, the voltage across the pack will be monitored to ensure they are not overcharged. During flight, the pack will also have a BMS and temperature monitoring system to manage the temperature of cells in the pack. This information will be passed to a microcontroller that the pilot can read externally. The second path of the block diagram is the cell power. The batteries will power a motor controller that manages the power input to the motor.

## 2.1 (b) Overview Automated Testbench Software Architecture

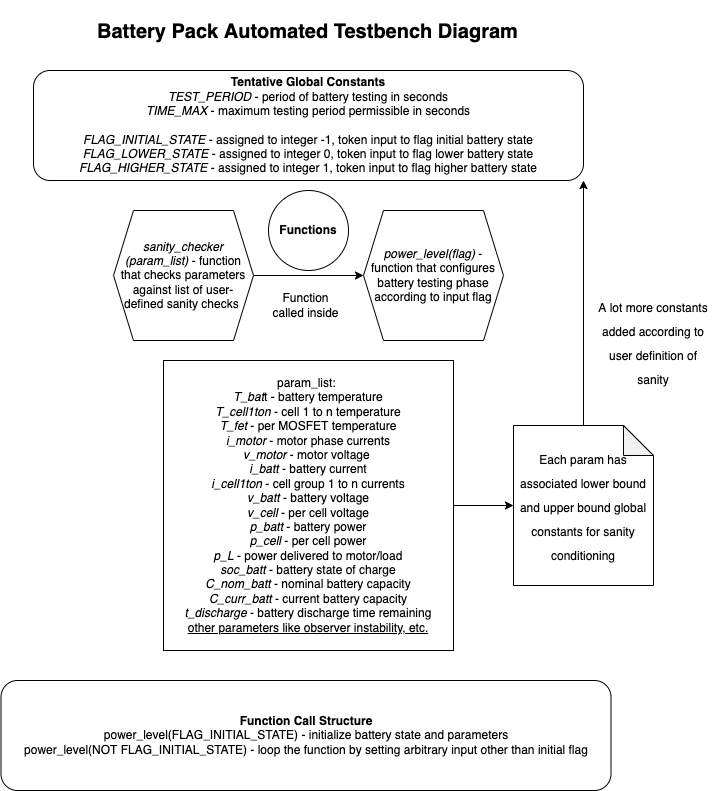
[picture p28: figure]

Figure 4: Battery pack automated testbench diagram using modified UML (Universal Modeling Language) syntax.

The testbench code should have some loop with at least four “top-view” conditions (a.k.a. battery monitoring sanity checks) and then it should have some actuation mechanism where as long as those conditions are satisfied, then the next phase of testing will begin according to the state variable or parameter list. So, the top view diagram provided above lists the definitions and relations between the following relevant battery testing parameters:

- t_test - Testing period (time set for testing that is measured in seconds and ranges from 0 to TIME_MAX), where TIME_MAX is some constant that is defined by the user or client accordingly
- user_stop - User-defined input (manual STOP command of testing)
- sane & insane - Sane state is that which meets the conditions involving each parameter outlined below, and insane is that which doesn't otherwise
  - T_batt (battery pack temperature, however it is defined), T_cell1, T_cell2,..., T_celln (temperature of each cell as defined by the engineers)
  - T_fet (MCU MOSFET temperature)
  - i_motor (motor phase currents)
  - v_motor (motor voltage)
  - i_batt (battery current), i_cell1, ... , i_celln (given cell group current)
  - v_batt (battery voltage) and v_cell (per cell voltage)
  - p_batt (battery power), p_cell (per cell power), p_L (current power delivered to load/motor)
  - SOC_batt (battery state of charge)
  - C_nom_batt (nominal capacity of battery), C_current (current capacity of battery)
  - t_discharge (time remaining for battery to discharge)

As for the functions used in the diagram:

- power_level(flag) - A power level function that sets relevant parameters according to some input token (“flag”)
  - the power level function determines the initial state of the battery and sets the relevant parameters (initial values)
  - the input token determines whether or not the test transitions to a higher or lower power level or shuts down
  - the function prints relevant parameters to the console for debugging and even manipulate some data if needed
- sanity_checker(param_list) - A sanity check function that evaluates the current battery state and set its values according to a number of conditions
  - the sanity checks are conditions that are defined such that some flag token is set to some value corresponding to sane or insane
  - either power level function is called in the sanity check function (or vice-versa possible) to parse the sane/insane flag inputs and transition the power level according to that flag token. If the flag input is sane, then power is transitioned to higher level, and otherwise, if it's insane, then the power is transitioned to lower level
  - in the definition of the sanity check function, the function itself is called again in order for it to loop indefinitely according to some sleep frequency (similar to void loop in Arduino IDE)

After defining the power level function and sanity check function in the lisp script, the power level function would be first called with the corresponding input token for initializing the battery state and determining its relevant parameters (i.e. it runs once similar to void setup in Arduino IDE). Then, the sanity check function would be directly called with the outputs of the power level function as its inputs.

## 2.2 User interface

Our user interface will be a simple LED indicator which will signal any errors in the pack. When the battery management system or temperature sensor detects any problems in the pack, the fault will be sent to the microcontroller which will prompt the LED indicator to turn on. This indicator will be placed in the cockpit so the pilot will be aware of any issues during flight.

A separate, second indicator will be used for charging the batteries. This indicator will turn green if the battery is charging properly. If the battery cells have a voltage imbalance, the indicator will change color notifying the user of an error. This signal will be communicated from the microcontroller managing the charging and sent to the LED indicator.

## 2.3 Physical description

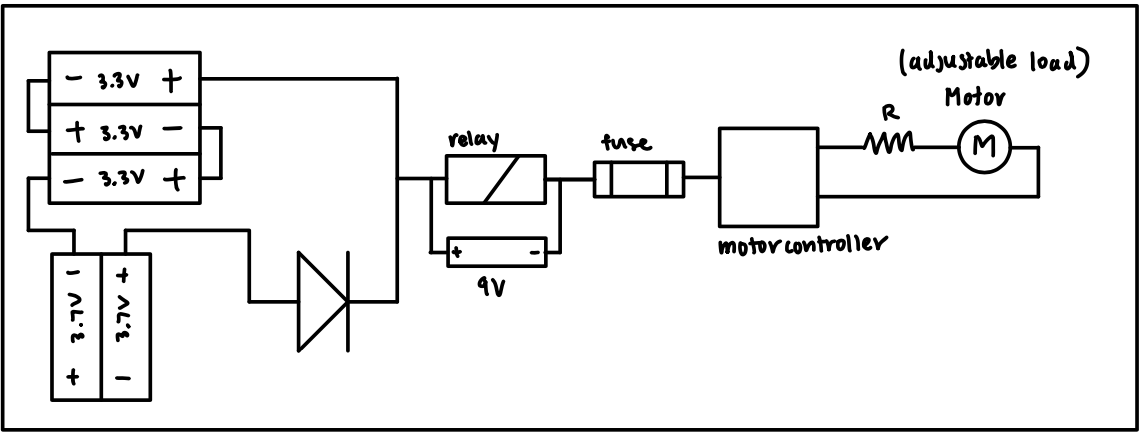
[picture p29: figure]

Figure 5: Final battery testing schematic.

## 2.4 Installation, setup, and support

The following software packages are needed before proceeding with the software configuration instructions:

- VESC Tool (free version) GUI developed by Benjamin Vedder
  - Qt Toolkit
  - .zip file extractor (Windows, Linux, Mac OS X, and Android supported like WinZip or 7-Zip)
  - Source code: https://github.com/vedderb/vesc_tool
- VESC-Lisp, Common Lisp, or LispBM Scripts
  - ANSI Common Lisp GNU v2.49 (2010-07-07 build) compiler (REPL)
  - For Mac OS X, install via MacPorts
  - For Windows and Linux (Ubuntu, Debian, Sun Solaris, etc.), install directly from https://clisp.sourceforge.io/
- Arduino IDE v1.8.19
  - Supported for Windows 7+, Linux (32-bit & 64-bit), Mac OS X (10.10 or newer), ChromeOS
  - Download directly from https://www.arduino.cc/en/software
- Arduino C/C++ Scripts (sketches)
  - Firmata library for all boards
  - LiquidCrystal.h library – optional for LCD display of temperature logs

The following pre-testing instructions must be followed to assemble the hardware and configure the software:

- Battery testing circuit hardware side
  - Connect 12 V lab DC power supply to the bottom left terminal of the 30 A relay using alligator or crocodile clips
  - Connect 9 V battery to the relay (top left and right connections) by soldering battery snap connectors to power it up and connect other 9 V battery to the current sensor using battery snap connectors to also power it up
  - Place each of the three LFP batteries in their respective single slot battery holders
  - Place both Li-ion batteries in the dual slot battery holder
  - Solder the wires connecting the LFP battery holder contacts in series and solder the first ring terminal wire to one of the LFP battery holders accordingly and the other to the Li-ion dual battery holder to create the parallel connection
  - Connect the ring terminal connected to the LFP battery holders into terminal ~C (phase-C) of the rectifier and the other terminal (which is connected to Li-ion batteries) to terminal B-
  - Solder the LFP battery holder and rectifier junction into the 30 A relay’s bottom right terminal
  - Solder the 7 A fuse into the bottom-right terminal of the Li-ion battery holder and connect its other end to the negative top terminal of the current sensor
  - Connect the positive top terminal of the current sensor to the motor controller positive XT30 connection; the negative terminal of this connection should be connected to the multimeter accordingly for voltage readings
  - Connect the positive terminal of the motor controller MR30 connector into the positive terminal of the multimeter to complete the connection for motor controller voltage readings
  - Connect the A50S motor controller to the laptop using micoUSB-USB cable
  - Connect the pico-clasp connector shell to MR30 connector, and connect that to the brushless motor’s connector
  - Connect the positive and negative terminals of the motor controller-motor junction to the positive and negative terminals of the power resistor respectively
- Adafruit Huzzah ESP32 microcontroller
  - Connect ESP32 to computer with microUSB-USB cable (if using a laptop with only USB-C ports, then a USB to USB-C hyperdrive or an adapter)
- Arduino Nano microcontroller hardware side
  - Connect Arduino Nano to computer with microUSB-USB cable (if using a laptop with only USB-C ports, then a USB to USB-C hyperdrive is needed)
  - Since resistors are blind to polarity, the thermistor and resistor ends are arbitrary, so for clarification, let one end be (a) and the other be (b) for both respectively
  - Connect pin #27 (5V DC power) to end (a) of 10K resistor, and connect end (b) of the resistor to end (a) of thermistor using male-to-male jumper wires
  - Connect pin #19 (A0/D14) to end (a) of thermistor using male-to-male jumper wires
  - Connect pin #29 (GND) to end (b) of thermistor using male-to-male jumper wires
- VESC Tool setup software side
  - Create an account on https://vesc-project.com/ > click on “VESC tool’ tab > purchase VESC Tool Free for €0.00 (no billing information required) > click on “Purchased Files” link (top right corner) > download and extract “vesc_tool_BETA_ALL.zip” (or for Windows users, download “vesc_tool_free_windows.zip”)
  - Alternatively install directly via source code: https://github.com/vedderb/vesc_tool
  - For Windows and Linux users, Install REPL Lisp compiler via SourceForge
  - For Mac OS X users install MacPorts v2.7.1
    - Install Xcode and Xcode Command Line Tools
    - Agree to Xcode license in Terminal: sudo xcodebuild -license
    - Install MacPorts according to version of OS X (convenient installation through .pkg installer for version 10.15+) on https://www.macports.org/install.php
    - After MacPorts installation, type sudo port install clisp to install common lisp implementation (interpreter, compiler, debugger, etc.)
- Arduino IDE software side
  - Go to Tools > Manage Libraries > Drop-down “Type” > Installed. Double-check that Firmata built-in library is uncorrupted and installed properly. For LCD temperature display option, if not already installed, search for LiquidCrystal and install version 1.0.6
  - For microcontroller testing, go to Tools > select Boards Manager > search for Arduino AVR Boards > ensure most up-to-date version installed (v1.8.5 as of in-lab testing) > select Board: Arduino Nano > under same tab, select appropriate serial port when board is connected
  - Once Arduino board is properly connected with aforementioned hardware configuration on breadboard, run the temperature logging Arduino code and check the serial monitor for logged temperature readings – modify sampling rate as appropriate. As a quick test, check that room temperature is properly recorded
- Qt Creator
  - Install Qt Creator using an open source development link. The link will automatically detect between Mac OS or Windows user:

https://www.qt.io/download-qt-installer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

  - Open BatteryDisplay file after successful installation
  - Build and run the app
  - Make sure you compile instruction for data you want to send through BLE on the EPS32 using Arduino IDE
  - Scan for device on the BatteryDisplay app and connect to ESP32 through BLE
  - Check to see if data are being received from ESP32, make sure the command execution are sent to the ESP32 through Arduino
- Diode, 9 V batteries, and properly soldered electrical connection testing (if necessary)
  - Test the voltages/currents (using a multimeter) across the terminals of the Schottky junction diode and the 9V batteries, as well as other electrical connections in the circuit to ensure that the connections are not faulty, i.e. improperly soldered or connected
- Electrical insulation of electrical contacts
  - Ensure that any exposed metallic wire ends are properly insulated for safety purposes
  - Coat sufficient amount of tape – typically used black electrical insulating tape – fully around metallic wire ends
  - Confirm that insulating tape does not disrupt the functioning of other electrical components for testing.

The following testing instructions must be followed to test battery functionality according to given specifications.

1. Assemble the circuit based on the aforementioned pre-testing instructions (make sure all components are available)
2. Connect the fuse relay with the power resistors in series, feeding into the power supply and parallel to the dual battery packs (Lithium-ion and LFP)
3. Allow the the thermistor to be in contact with each battery for two seconds to get temperature readings
4. Wire the motor controller directly to the thermocouple digital thermometer for the separate temperature monitoring system accordingly (for alternate temperature sensing, use a thermal IR camera)
5. Setup the multimeter connection point to probe points as close to the motor speed controller as possible (this is due to the voltage drop across the wires at higher amps)
6. Connect the motor controller with the computer by clicking “connect” on the right hand side of the VESC tool, then under the window on the left-hand side, select RT (real-time data) and on top, select the current tab to display the current-time plots for the battery and the motor controller
7. Begin the test experiment by closing the relay in the circuit and manually adjusting i_motor (motor current) at the bottom left corner of the VESC tool from 0 A to 15 A, until the battery current i_batt reaches 5A in conjunction. Note that VESC software handles the temperature logging of the MOSFETs on the motor controller, and that this can be found on the top under the temperature tab
  a. Record the current readings of each battery pack circuit frequently and continue to monitor the temperature.

# 3 Operation of the Project

## 3.1 Operating Mode I: Normal Operation

Discharging

- Carry the battery pack into the eGlider
- Plug the connector to the electric motor
- Check the thermistor to prevent the battery pack from overheating

Charging

- Carry out the battery pack from the eGlider
- Plug the connector from the wall to the battery pack
- Check the thermistors to prevent the battery pack from overheating

## 3.2 Operating Mode II: Abnormal Operation

Hardware errors

- If the battery cells swell, unplug the charging connector and the discharging connector.
- If the thermistor sensor detects a high temperature inside the battery pack, unplug the connector from the battery to the motor.
- If the battery cells are physically damaged, stop using the battery pack and request repair and replacement services.
- If the battery cell leaks, stop using the battery pack and ask for repair and replacement services.
- If the battery pack is dropped from 1 meter or higher, check whether the battery cells and PCB are in place or not.
- If the battery pack did not charge properly, stop using the battery pack
- If the battery pack did not discharge properly, stop using the battery pack

## 3.3 Safety Issues

- Users should be careful to not spill liquids into the battery pack. PCB, batteries, and thermistor may be damaged by liquids
- Users should not try to repair the unit by themselves. Contact a local supplier for more details when the packet needs to be replaced
- If the user tries to replace the batteries, replace them with batteries of the same quantity, type, and capacity

Storage

- Battery pack should be stored away from liquids to avoid potential damage. Liquids may cause a short circuit damaging the PCB, batteries, and thermistor.
- Battery pack should be stored away from the combustible materials.
- Battery pack should be stored at temperatures between -40 degrees celsius and 60 degrees celsius .
- Battery pack should be stored away from anything that can catch fire.
- Battery pack should not be stored out of direct sunlight.
- Battery pack should be removed from the device when no longer in use.
- Inspect the status of the battery pack at least weekly.

Charging

- Use a certified input power cable with the correct plugs and sockets to charge the battery pack.
- Do not overcharge or over-discharge the battery.
- Inspect charging signs of the battery pack before charging.
- Check the voltage status of the battery before attaching it to the device.
- Users should only attach the battery pack to the device to satisfy the design requirements. Check the parameter requirements of the device such as power, minimum current flow, maximum current flow, etc.
- Battery pack should be recharged every time it is used

Disposal

- Dispose of a battery pack that no longer holds substantial charge or has physical damage.
- Do not dispose of the battery pack in a regular trash can. Discard the battery pack in a facility capable of cell recycling.
- Do not dispose of the battery pack in an open fire. The battery pack may explode.

# 4 Technical Background

The battery pack is designed exclusively for eGlider power storage. Any uses outside of this were not taken into consideration during development.

Our approach to solving the problem of eGlider battery storage hinges on the dual chemistry approach of the battery pack. The dual chemistry of our battery pack allows it to use about 80% of its total stored energy during take off as opposed to the industry standard which only uses about 20%. For safety reasons, it is important to use most of a battery pack's stored energy upon launch because in the event of a fire, the temperature and intensity of the fire would be proportional to the remaining energy stored in the battery pack.

We rely on a small pack of LFP 19s1p batteries for early take off in conjunction with a pack of Li-ion batteries which powers the rest of the flight. Both of these batteries were chosen for their specific chemical characteristics. LFP batteries were chosen to power the early takeoff stage because they have a very high continuous discharge rate of ~50A and can supply up to 120A in short bursts. LFP batteries are also very chemically robust, which allows them to handle deep discharges unachievable by Li-ion batteries.

For the late climbing portion of takeoff we rely on a pack of Li-ion 12s8p batteries to provide the bulk of the current, which is expected to be about 200A and decaying down to about 100A over the course of a flight. While LFP will provide fast sourcing, the Li-ion pack’s high energy density will provide the energy needed to reach cruising altitude. Due to the size of the pack, each battery will have ~25A max current on it, which is within their continuous current range.

In addition to the batteries we have also designed supplemental electronic systems to monitor the pack, reduce losses, and notify the pilot. These systems include a temperature sensing system, an ideal diode system, and a pilot interface. We have designed a temperature sensing system for use with a microcontroller carrying ADC units. An issue common with temperature sensing through the use of microcontroller ADCs is that individual thermistors do not scale well. Generally, one ADC pin is needed for each temperature sensor. Microcontrollers typically have around 10 ADC pins, allowing for 10 temperature points on the battery packs. This is insufficient for larger battery packs because a temperature point is needed on every cell to determine cell failures and give advanced warning to the pilot. Our modular approach uses a buffer mosfet and flip-flop ic’s to switch through a string of thermistors using a single ADC. This hardware and code solution solves the ADC problem and has the added benefit of being modular with the potential to be expanded into industries beyond the scope of our project.

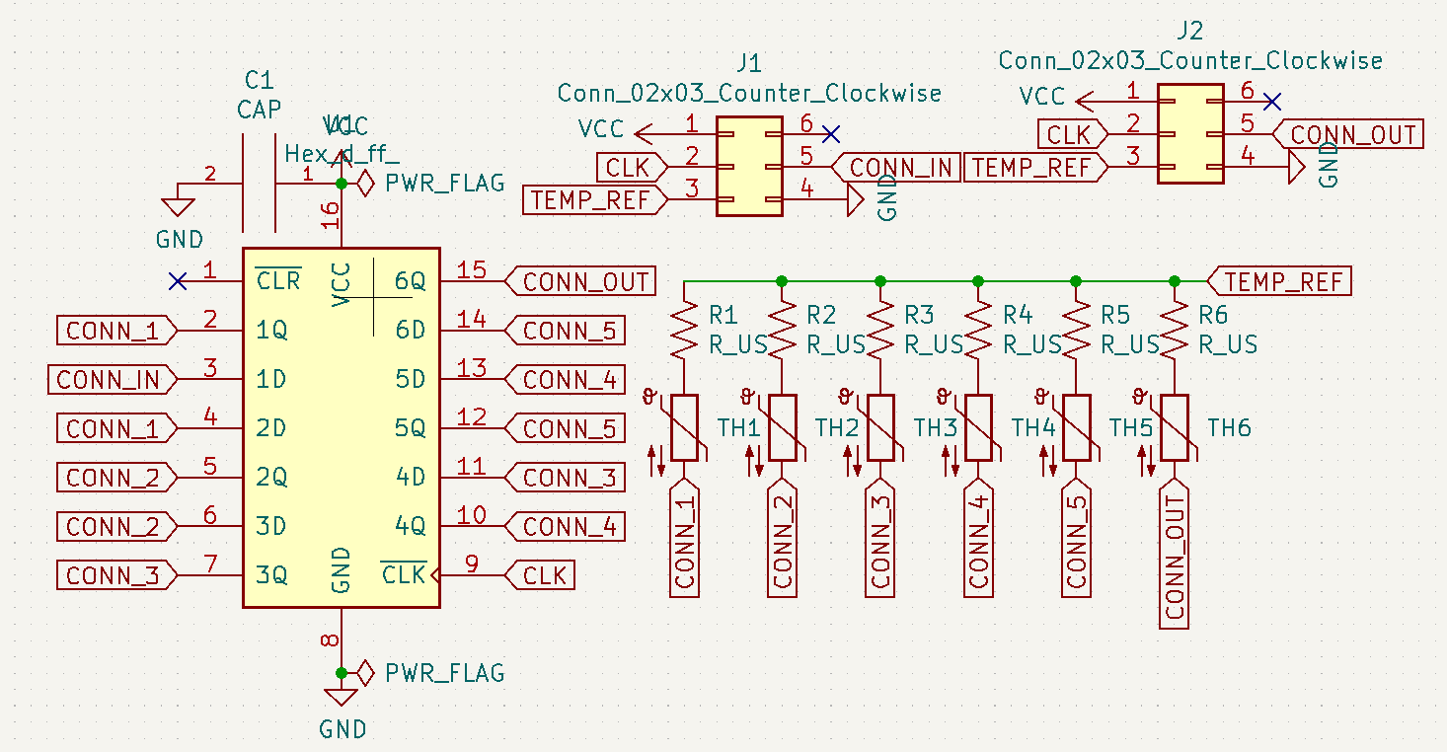
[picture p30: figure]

Figure 6: Modular thermistor sampling schematic with connections to micontroller (conn_in, clk, vcc, gnd).

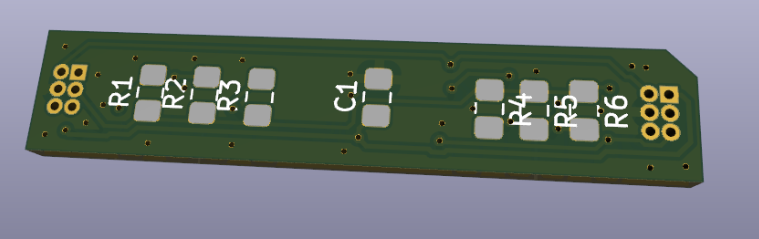
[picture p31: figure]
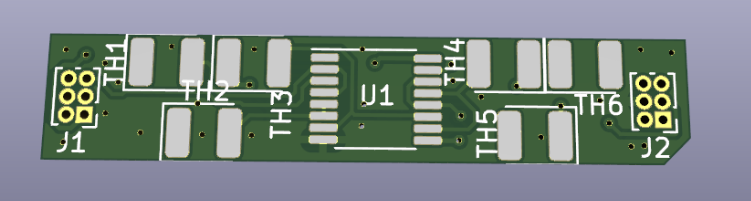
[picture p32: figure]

Figure 7: Back (left) and front (right) PCB renders for temperature sensing thermistor modules.

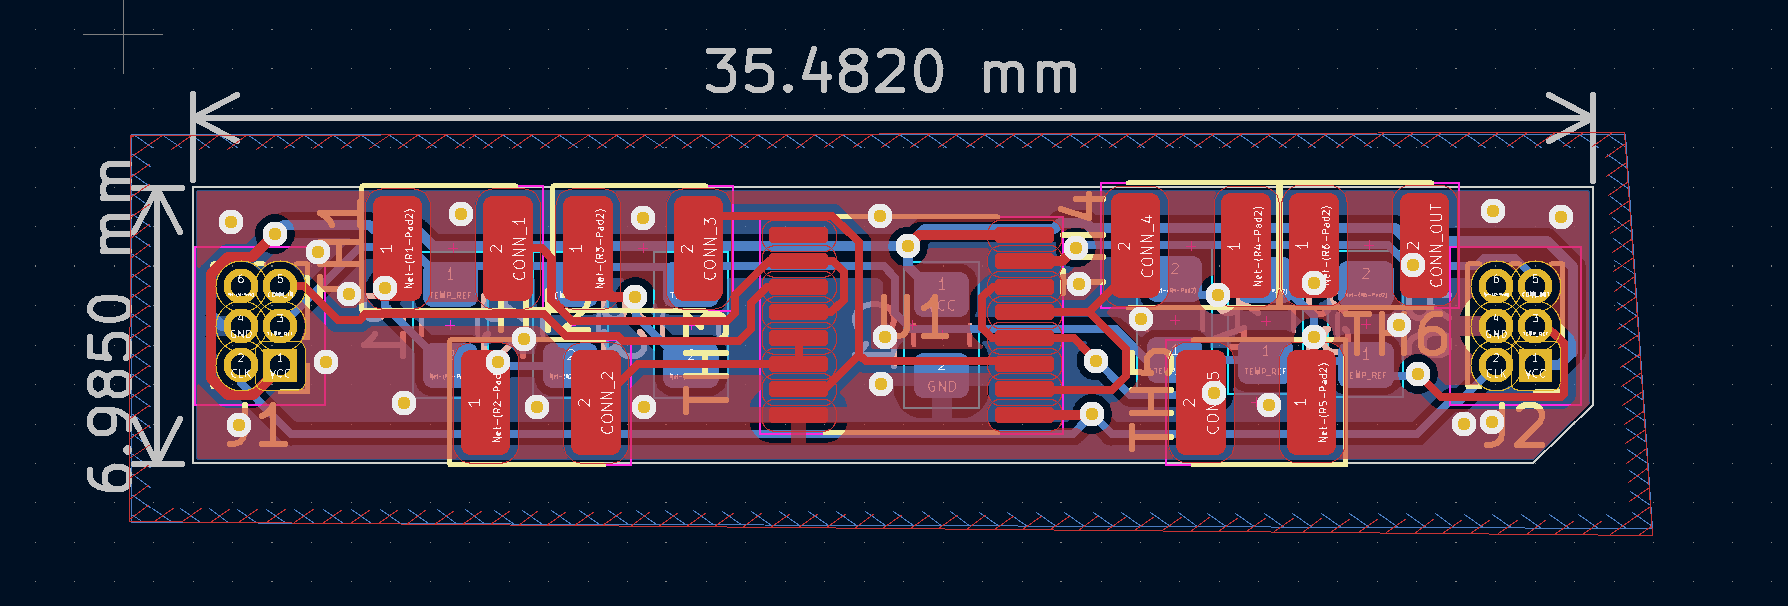
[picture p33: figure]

Figure 8: PCB Layout for thermistor temperature sensing modules designed for between cell installation.

Size is the largest issue when it comes to the design of these boards, they are built to fit in between the battery cells in the pack to limit the wire strains and prevent accidental disconnection.

Since we are using a battery configuration of 19s1p for the LFP and 12s8p for the Li-ion battery the nominal voltages are 68.4V and 50.4V respectively, leading to an issue of back feeding current from the LFP batteries to the Li-ion pack. This can be rectified through the use of a diode. One issue with using the diode is power loss, with a high current schottky diode the losses can be expected to surpass 100 Watts. Rather than using a conventional diode we can use what is known as an “ideal diode”. Through the use of an ideal diode controller and three high current mosfets we create a system that works the same way as a diode without the same losses associated. Once the LFP pack reaches the voltage of the Li-ion pack, the ideal diode controller produces a voltage at the gate of the mosfet turning it on and allowing current to flow to the motor controller from the Li-ion batteries.

The PCB for our ideal diode board needs to be designed differently than conventional PCBs. Since the MOSFET array will need to carry up to 300A we cannot use conventional PCB traces to transmit power which generally have a maximum current rating of about 10A. We handle the high current by soldering copper bus bars onto 6 mm traces. High current also leads to the problem of heat dissipation. To manage this problem, there are two copper pours on the top and bottom layers to distribute the heat evenly acting as a heatsink. The PCB also has a conventional heat sink to help with the heat dissipation requirements.

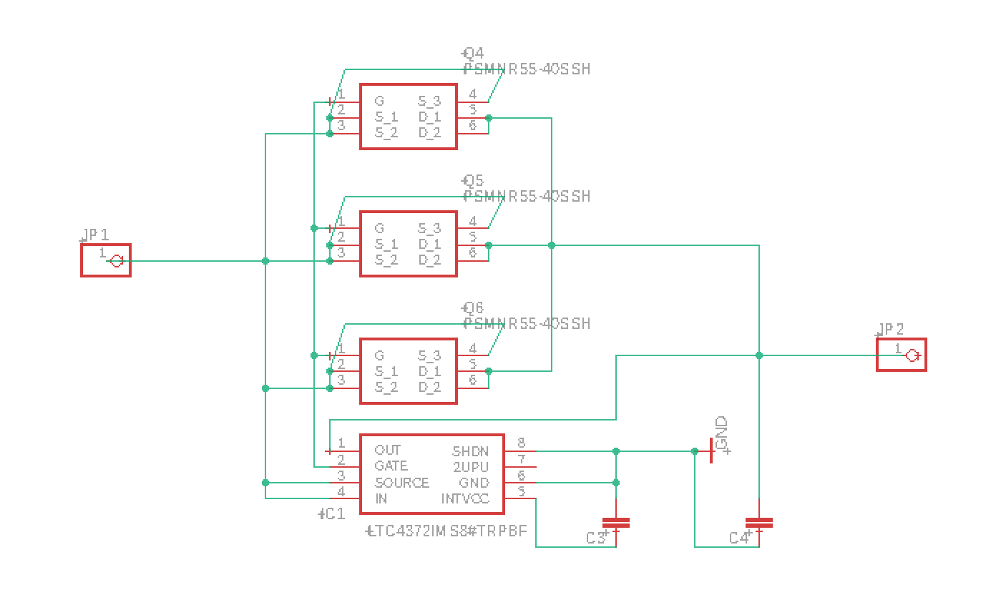
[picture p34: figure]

Figure 9: Ideal diode controller PCB schematic.

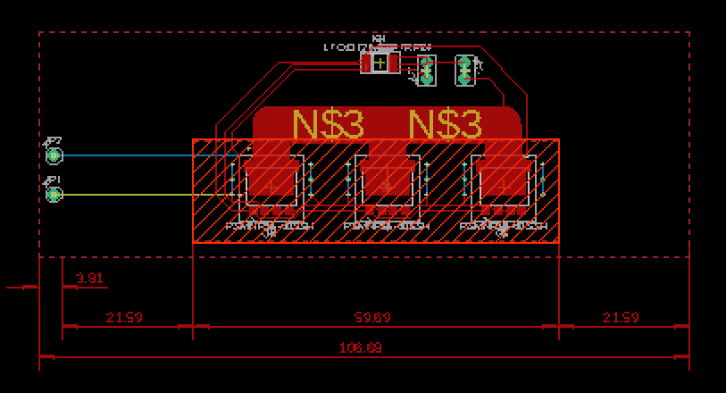
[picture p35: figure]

Figure 10: Ideal diode controller PCB board.

To charge the batteries the final pack will require two charging ports, one for each separate chemistry battery pack. These chargers need to be bought from an external vendor and need to be able to handle the voltages and charging schedule needed for each of the two chemistries. This is important because different chemistry batteries require different charging algorithms to ensure the longest battery life and limit degradation.

# 5 Relevant Engineering Standards

FMEA Analysis

According to the Cambridge Institute for Healthcare Improvement, Failure Modes and Effects Analysis (FMEA) is a proactive method for identifying potential points of failure in a process. The method is used to: (a) evaluate a process to identify where and how it might fail and (b) to assess the relative impact of different failures in order to highlight the elements that pose the greatest amount of risk and consequently that need to be changed. There are several parameters involved: (1) probability that a failure would occur (occurrence), (2) severity of the failure, (3) detection of the failure, (4) risk priority number in accordance with a criticality matrix, and (5) remarks/mitigation/actions. It is necessary to systematically analyze the safety of the first test for the LFP pack before making the full size hybrid battery pack. An integral scale from "1" to "10" has been established for evaluating each of the failure components listed previously according to Figure 11.

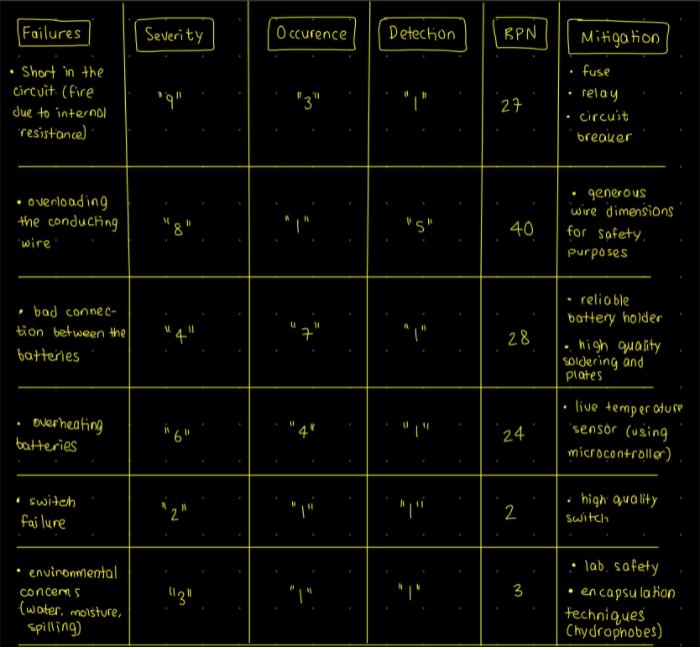
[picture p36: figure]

Figure 11: FMEA Analysis table for hybrid battery pack testing.

The risk priority number (RPN) has been calculated using the following equation:

RPN = Severity ×Occurrence ×Detection

The table illustrates that overloading the conducting wire, bad battery connections, and a possible short in the circuit should take highest priority. The first failure concern can be addressed by providing generous wire dimensions to handle about 550A (calculated from an internal resistance of 6 mΩ and a net voltage of 9.9V, with each battery having a voltage of 3.3V).

Oracle Javadoc Style Programming Documentation

One of the most important factors in any written program is how it is documented and organized. A program that follows a consistent style of both documentation and code formatting is easier to read, understand, debug, and maintain. The Oracle Javadoc is one of the most commonly used documentation styles for large-scale software systems, and as such, this was implemented in the testbench code. In the Lisp scripts, all constants are all fully capitalized (e.g. TEST-PERIOD denotes the constant value for the battery testing period in seconds). Whereas, variable identifiers are all set to lowercase letters separated by dashes rather than underscores (e.g. i-motor denotes the motor current in Amps). By engineering standards, underscores are used, but Lisp does not permit the use of underscores for variable identifiers as the underscore character is used for pattern matching algorithms, so dashes are the “modified” variable identifier standard for Lisp. Function identifiers follow the same standard as variable identifiers, with the same exception of underscores replaced with dashes in Lisp (e.g. power-level(flag) denotes the power level transition function identifier). Every source file has a comment block at the top that contains relevant information. As per Javadoc style, the script contains a brief description of source code’s purpose at the top. For the file name, author, affiliation, and version number, the following tags are used respectively: @file [filename], @author [author name], @affiliation [affiliation], and @version [version number]. For generic comment style, three “;” are used to describe the header comment block, global constant group comment blocks, and function definition comment blocks. Then, single-line comments are denoted using single “;”. With regards to the function definition comment blocks, the function purpose is first described, then each input parameter the function takes is included on a separate line using the tag @param [parameter name] [parameter description]. The output parameters (or the values returned by the function) are denoted, also on separate lines, using the tag @return [return name] [return description].

# 6 Cost Breakdown

Project Costs for Production of Beta Version[^1]
Item | Quantity | Description | Unit Cost ($) | Extended Cost ($)
1 | 19 | LiFePO4 | 14 | 266
2 | 96 | Li-ion | 8.53 | 818.56
5 | 1 | Ideal Diode Controller | 7.9 | 7.90
6 | 10 ft | 4/0 AWG Wires (5 ft) | 50 | 100
7 | 21 | PCB Battery Temperature Sensing | 1.65 | 34.65
8 | 1 | 1 µF Capacitor for ideal Diode | 0.28 | 0.28
9 | 1 | MOSFET for Ideal Diode | 6.44 | 6.44
10 | 1 | 0.1 µF Capacitor for ideal Diode | 1.07 | 1.07
11 | 1 | Uxcell NTC Thermistors Resistor MF52-103/3435 10K Ohm Temperature Sensor Pack of 60 | 9.99 | 9.99
12 | 1 | Adafruit Huzzah ESP32 | 24.61 | 24.61
Total Cost ($) | | | | 1,237.10

The beta product estimated cost breakdown of the hybrid battery pack will consist of all hardware components required to realize the full version of our battery design.

The main expense of the project will be coming from the two different battery cells, LFP 19s1p setup ($266) and Li-ion 12s8p ($818.56). The rest of the product design component will have a diode controller ($7.90), thermistors ($9.99), an Adafruit Huzzah ESP32 ($24.61) and two different PCBs – one for the ideal diode ($7.50) and 20 for the temperature sensing of the battery pack ($34.65). The battery pack will also be wired with a stronger kind capable of handling 300A rated between 2/0 - 4/0 AWG (~$100).

As for software we use to make the heatmap display we are using an open source software application called Qt creator which is free with no additional cost.

# 7 Appendices

## 7.1 Appendix A - Specifications

Requirement value, range, tolerance, units | Requirement value, range, tolerance, units

Temperature and Environment
Environmentals | - function between 0°C and 40°C - withstand temperatures between -20°C and 50°C
Normal discharge temperatures | - upper limit of 70°C - preference of 50°C
Target final SoC | - 5% for the LFP - 20% for the Li-ion

Energy
Self-launch time | - ~ 4 minutes
Target power profile | - 0s to 60s at >16 kW - 60s to 180s at ~12 kW - 180s to 300s at ~10 kW - 300s to 600s at ~6 kW
Target final SoC | - 5% for the LFP - 20% for the Li-ion
Power connector | - must handle 300A for 60s
Target voltage | - 60V peak under load
Battery Management System | - two different BMS for each pack

Physical Quantity
Target weight | - Goal: 10kg - Threshold: 12kg

Charging and Discharging
Initial discharge rate | - 300A
Final discharge rate | - 100A
Target cycle life | - threshold: 500 launches - goal: 1000 cycles
Precharging | - handled by exterior components
Charge connectors | - each cell must be individually accessible for balancing purposes

## 7.2 Appendix B – Team Information

Team #23: HYP Batteries consists of Spencer P. Piligian, Daniel Kao, Yusheng Chen, Steven Wang, and Ismaeel AlAlawi. We are a team of five electrical engineers working on HYP batteries. This project aims to help us further develop our technical skills and knowledge in both the hardware & circuit design space and embedded software prototyping.

Post-Graduation Plans:

Spencer P. Piligian

B.S Electrical Engineering

Career: General Motors TRACK Engineer

Daniel Kao

B.S Electrical Engineering

Career: Undecided

Yusheng Chen

B.S Electrical Engineering

Career: Master’s at Columbia University

Steven Wang

B.S Electrical Engineering

Career: General Dynamics, Systems Engineer II

Ismaeel AlAlawi

B.S Electrical Engineering

Career: Undecided

[^1] The beta version is the third prototype (the product that comes after the second prototype testing).

Team #23 (HYP Batteries) April 18, 2022

Technical Progress Report

User's Manual

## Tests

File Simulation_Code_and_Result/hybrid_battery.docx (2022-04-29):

2021/11/15 EF1:46

Hybrid battery analysis Final - Jupyter Notebook

In [2147]:

using Plots using CSV using DataFrames using Interpolations

In [2148]:

# Import battery performance data (taken from graphs and generated by Engauge) csv_diamond_05C = CSV.File("Foxtech Diamond/Diamond cell test, 0.5C.csv") df_diamond_05C = DataFrame(csv_diamond_05C) itp_diamond_05C = LinearInterpolation(df_diamond_05C.Ahr, df_diamond_05C.V, extrapolation_b

csv_diamond_3C = CSV. File("Foxtech Diamond/Diamond cell test, 3C.csv") df_diamond_3C = DataFrame(csv_diamond_3C) itp_diamond_3C = LinearInterpolation(df_diamond_3C.Ahr, df_diamond_3C.V, extrapolation_bc=L

csv_diamond_5C = CSV.File("Foxtech Diamond/Diamond cell test, 5C.csv") df_diamond_5C = DataFrame(csv_diamond_5C) itp_diamond_5C = LinearInterpolation(df_diamond_5C.Ahr, df_diamond_5C.V, extrapolation_bc=L

## IMPORTANT TO UPDATE WHENEVER THE BATTERY DATASHEETS ARE CHANGED ## The order is important, it must be done in sequential order by growing discharge rate discharge_curves_diamond = (

(0.5, itp_diamond_05C), (3.0, itp_diamond_3C), (5.0, itp_diamond_5C)

# Capacity of cells in datasheet, in [Ahr] ahr_datasheet_diamond_cell = 22

# Individual cell max discharge rate c_diamond_max = 5.5

Out[2148]:

5.5

localhost:8888/notebooks/SENIOR DESIGN SIMULATION ALL/11/11_9/Hybrid battery analysis Final.ipynb

1/20

2021/11/15 EF1:46

Hybrid battery analysis Final - Jupyter Notebook

In [2149]:

# Import battery performance data (taken from graphs and generated by Engauge) csv_lipo_O_84C = CSV. File("Molicel/P42A/P42A, O_84C.csv") df_lipo_0_84C = DataFrame (csv_lipo_O_84C) itp_lipo_0_84C = LinearInterpolation(df_lipo_0_84C.Ahr, df_lipo_O_840.V, extrapolation_bc=L

csv_lipo_4_2C = CSV.File("Molicel/P42A/P42A, 4_20.csv") df_lipo_4_2C = DataFrame(csv_lipo_4_20) itp_lipo_4_2C = LinearInterpolation(df_lipo_4_2C.Ahr, df_lipo_4_2C.V, extrapolation_bc=Line

csv_lipo_10C = CSV.File("Molicel/P42A/P42A, 10C.csv") df_lipo_10C = DataFrame(csv_lipo_10C) itp_lipo_10C = LinearInterpolation(df_lipo_10C.Ahr, df_lipo_10C.V, extrapolation_bc=Line())

csv_lipo_20C = CSV.File("Molicel/P42A/P42A, 200.csv") df_lipo_20C = DataFrame(csv_lipo_200) itp_lipo_20C = LinearInterpolation(df_lipo_20C. Ahr, df_lipo_28C.V, extrapolation_bc=Line())

csv_lipo_30C = CSV.File("Molicel/P42A/P42A, 300.csv") df_lipo_30C = DataFrame(csv_lipo_30C)

itp_lipo_30C = LinearInterpolation(df_lipo_30C.Ahr, df_lipo_30C.V, extrapolation_bc=Line())

## IMPORTANT TO UPDATE WHENEVER THE BATTERY DATASHEETS ARE CHANGED ## The order is important, it must be done in sequential order by growing discharge rate discharge_curves_P42A = (

(0.84, itp_lipo_0_84C), (4.2, itp_lipo_4_20), (10.0, itp_lipo_100), (20.0, itp_lipo_200), (30.0, itp_lipo_30C)

# Capacity of cells in datasheet, in [Ahr] ahr_datasheet_P42A_cell = 4.2

# Individual cell mass, in [kg] mass_P42A_cell = 0.070

# Individual cell max continuous discharge rate. This is taken from testing at https://www. C_P42A_max = 45/ahr_datasheet_P42A_cell

# Individual cell nominal energy capacity, in [kwhr] kwhr_P42A_cell = .0147

Out[2149]:

0.0147

localhost:8888/notebooks/SENIOR DESIGN SIMULATION ALL/11/11_9/Hybrid battery analysis Final.ipynb

2/20

2021/11/15 EF1:46

Hybrid battery analysis Final - Jupyter Notebook

In [2150]:

# Import battery performance data (taken from graphs and generated by Engauge) csv_lipo_0_84C = CSV. File("Molicel/P26A/P26A,Q_520.csv") df_lipo_O_84C = DataFrame(csv_lipo_O_84C) itp_lipo_0_84C = LinearInterpolation(df_lipo_0_84C.Ahr, df_lipo_O_840.V, extrapolation_bc=L

csv_lipo_10C = CSV. File("Molicel/P26A/P26A, 10C.csv") df_lipo_10C = DataFrame(csv_lipo_10C) itp_lipo_10C = LinearInterpolation(df_lipo_10C.Ahr, df_lipo_10C.V, extrapolation_bc=Line())

csv_lipo_12_6C = CSV. File("Molicel/P26A/P26A, 12_6C.csv") df_lipo_12_6C = DataFrame (csv_lipo_12_6C) itp_lipo_12_6C= LinearInterpolation(df_lipo_12_6C.Ahr, df_lipo_12_6C.V, extrapolation_bc=Li

csv_lipo_20C = CSV. File("Molicel/P26A/P26A, 200.csv") df_lipo_20C = DataFrame(csv_lipo_200) itp_lipo_20C = LinearInterpolation(df_lipo_20C.Ahr, df_lipo_20C.V, extrapolation_bc=Line())

## IMPORTANT TO UPDATE WHENEVER THE BATTERY DATASHEETS ARE CHANGED ## The order is important, it must be done in sequential order by growing discharge rate discharge_curves_P26C=(

(0.84, itp_lipo_0_84C), (4.2, itp_lipo_4_2C), (10.0, itp_lipo_10C), (20.0, itp_lipo_200), (30.0, itp_lipo_30C)

# Capacity of cells in datasheet, in [Ahr] ahr_datasheet_P26_cell = 2.6

# Individual cell mass, in [kg] mass_P26_cell = 0.05

# Individual cell max discharge rate C_P26_max = 35/ahr_datasheet_P26_cell

# Individual cell nominal energy capacity, in [kwhr] kwhr_P26_cell = .095

Out[2150]:

0.095

localhost:8888/notebooks/SENIOR DESIGN SIMULATION ALL/11/11_9/Hybrid battery analysis Final.ipynb

3/20

2021/11/15 EF1:46

Hybrid battery analysis Final - Jupyter Notebook

In [2151]:

# Import battery performance data (taken from graphs and generated by Engauge) # A123Systems cells. Probably shouldn't be changed csv_a123_1C = CSV.File("A123Systems/ANR26650M1B, 1C.csv") df_a123_1C = DataFrame(csv_a123_10) itp_a123_1C = LinearInterpolation(df_a123_1C.Ahr, df_a123_1C.V, extrapolation_bc=Line())

csv_a123_6C = CSV.File("A123Systems/ANR26650M1B, 6C.csv") df_a123_6C = DataFrame(csv_a123_6C) itp_a123_6C = LinearInterpolation(df_a123_6C.Ahr, df_a123_6C.V, extrapolation_bc=Line())

csv_a123_20C = CSV.File("A123Systems/ANR26650M1B, 200.csv") df_a123_20C = DataFrame(csv_a123_200) itp_a123_20C = LinearInterpolation(df_a123_20C.Ahr, df_a123_20C.V, extrapolation_bc=Line())

## IMPORTANT TO UPDATE WHENEVER THE BATTERIES DATASHEETS ARE CHANGED ## The order is important, it must be done in sequential order by growing discharge rate discharge_curves_a123 = (

(1.0, itp_a123_10), (6.0, itp_a123_6C), (20.0, itp_a123_200)

# Individual cell capacity, in [Ahr] ahr_a123_cell = 2.65

# Individual cell mass, in [kg] mass_a123_cell = .076

# Individual cell max discharge rate c_a123_max = 50

# Individual cell nominal energy capacity, in [kwhr] kwhr_a123_cell = .00825

discharge_index_vector_a123 = getfield. (discharge_curves_a123, 1)

Out[2151]: (1.0, 6.0, 20.0)

localhost:8888/notebooks/SENIOR DESIGN SIMULATION ALL/11/11_9/Hybrid battery analysis Final.ipynb

4/20

2021/11/15 EF1:46

Hybrid battery analysis Final - Jupyter Notebook

In [2152]:

## Function definitions

# Finds the indices in A which bracket the argument, X. This assumes that A is an ordered s function findNearestBracket(A,x)

# find the index which is closest to the value tmpIdx = argmin(abs.(A .- x))

# Find the pair of indices which bracket the value if tmpIdx == 1

lowIdx = 1 highIdx = 2 elseif tmpIdx == length(A)

lowIdx = length(A)-1

highIdx = length(A) else

if A[tmpIdx] < x

lowIdx = tmpIdx highIdx = tmpIdx+1 else

lowIdx = tmpIdx-1 highIdx = tmpIdx end end

return [lowIdx, highIdx] end

# Calculate by interpolation the instantaneous pack voltage. It takes into account the disc function instantaneous_pack_voltage (discharge_vector, discharge_curves, c_battery, ahr_accu

idx = findNearestBracket(discharge_vector, c_battery) lowC = discharge_vector[idx[1]] high = discharge_vector[idx[2]]

v_instantaneous_lowC = discharge_curves [idx[1]][2] v_instantaneous_highc = discharge_curves[idx[2]][2] v_instantaneous = batt_v(c_battery, lowc, highc, v_instantaneous_lowc(ahr_accum_cell),

X

return v_instantaneous end

# Linear interpolation of the battery voltage, with discharge rate as the independent varia function batt_v(x, x1, x2, y1, y2)

m = (y2-y1)/(x2-x1)

y = m*(x-1) + y1 end

Out[2152]:

batt_v (generic function with 1 method)

User tunable parameters

localhost:8888/notebooks/SENIOR DESIGN SIMULATION ALL/11/11_9/Hybrid battery analysis Final.ipynb

5/20

2021/11/15 EF1:46

Hybrid battery analysis Final - Jupyter Notebook

In [2153]:

# pack = "Diamond" pack = "Molicel P42A" #pack = "Molicel P26A"

# Number of parallel cells in pack num_cols_a123 =1

# Number of series rows in pack num_rows_a123 -19

if pack == "Molicel P42A"

# Number of parallel cells in pack num_cols_lipo = 10 # Number of series rows in pack num_rows_lipo =12

elseif pack == "Molicel P26A"

# Number of parallel cells in pack

num_cols_lipo = 10

# Number of series rows in pack num_rows_lipo = 22

elseif pack == "Diamond"

ahr_diamond_cell = 16

# Can only equal 16, 22, or 30

# Number of parallel cells in pack num_cols_lipo = 1

# Number of series rows in pack num_rows_lipo = 12

end

Out[2153]:

12

localhost:8888/notebooks/SENIOR DESIGN SIMULATION ALL/11/11_9/Hybrid battery analysis Final.ipynb

6/20

2021/11/15 EF1:46

Hybrid battery analysis Final - Jupyter Notebook

In [2154]:

if pack == "Molicel P42A"

discharge_curves_lipo = discharge_curves_P42A; mass_lipo_cell = mass_P42A_cell

ahr_datasheet_lipo_cell = ahr_datasheet_P42A_cell ahr_lipo_cell = ahr_datasheet_P42A_cell kwhr_lipo_cell = kwhr_P42A_cell

c_lipo_max = C_P42A_max elseif pack == "Molicel P26A"

discharge_curves_lipo = discharge_curves_P26A; mass_lipo_cell = mass_P26A_cell ahr_datasheet_lipo_cell = ahr_datasheet_P26A_cell ahr_lipo_cell = ahr_datasheet_P26A_cell kwhr_lipo_cell = kwhr_P26A_cell

c_lipo_max = c_P26A_max elseif pack == "Diamond"

mass_diamond_cell = (1.500/6) * (ahr_diamond_cell/16) # Backed out from the Foxtech webp

# Individual cell nominal energy capacity, in [kwhr] kwhr_diamond_cell = .111 * (ahr_diamond_cell / ahr_datasheet_diamond_cell)

discharge_curves_lipo = discharge_curves_diamond; mass_lipo_cell = mass_diamond_cell

ahr_datasheet_lipo_cell = ahr_datasheet_diamond_cell ahr_lipo_cell = ahr_datasheet_diamond_cell kwhr_lipo_cell = kwhr_diamond_cell

c_lipo_max = c_diamond_max end

discharge_index_vector_lipo = getfield. (discharge_curves_lipo, 1)

Urves

Out[2154]:

(0.84, 4.2, 10.0, 20.0, 30.0)

In [2155]:

# Airplane MTOW airplaneMass = 300 climbVelocity = 55*.511 glideratio = 20

Out[2155]:

20

localhost:8888/notebooks/SENIOR DESIGN SIMULATION ALL/11/11_9/Hybrid battery analysis Final.ipynb

7/20

2021/11/15 EF1:46

Hybrid battery analysis Final - Jupyter Notebook

In [2156]: # Diode forward voltage drop # https://www.vishay.com/docs/93804/vs-175bqg030hf4.pdf v_drop_diode = 0.782

D

# Pack nominal energy capacity kwhr_a123_pack = kwhr_a123_cell * num_cols_a123 * num_rows_a123 kwhr_lipo_pack = kwhr_lipo_cell * num_cols_lipo * num_rows_lipo

# Pack amps parallel capacity ahr_a123_pack = ahr_a123_cell * num_cols_a123 ahr_lipo_pack = ahr_lipo_cell * num_cols_lipo

# Pack cell mass mass_a123_pack = mass_a123_cell * num_cols_a123 * num_rows_a123 mass_lipo_pack = mass_lipo_cell * num_cols_lipo * num_rows_lipo

pack_A_label = pack_B_label =

string("A123 LiFePo4 (", num_rows_a123, "S", num_cols_a123, "P)") string("Li-ion (", num_rows_lipo, "S, ", num_cols_lipo, "P,", round(ahr_lipo

println("mass [kg]: " * string(round.([mass_a123_pack mass_lipo_pack], digits = 1))) println("capacity [Ahr / kwHr]: " * string(round.([ahr_a123_pack kwhr_a123_pack; ahr_lipo

mass [kg]: [1.4 8.4] capacity [Ahr / kwHr]: [2.6 0.2; 42.0 1.8]

localhost:8888/notebooks/SENIOR DESIGN SIMULATION ALL/11/11_9/Hybrid battery analysis Final.ipynb

8/20

2021/11/15 EF1:46

Hybrid battery analysis Final - Jupyter Notebook

In [2157]:

# Simulate across time t = 0 delT = .05

# Power schedule P_TAKEOFF = 18e3 P_MAX_CONTINUOUS = 12e3 P_SUSTAIN_CLIMB = 10e3 P_SUSTAIN = 6e3

# Plotting variables t_experiment = Float64[] I_motor = Float64[] V_a123 = Float64[] V_lipo = Float64[] V_bus = Float64[] soc_a123_experiment = Float64[] soc_lipo_experiment = Float64[] c_a123_experiment = Float64[] c_lipo_experiment = Float64[] P_experiment = Float64[] P_a123 = Float64[] P_lipo = Float64[] E_a123 = Float64[] E_lipo = Float64[] Soc_20_lipo = 0 soc_5_a123 = 0 vel_airplane = [] hgt_airplane = [] hgt_dot_airplane = []

c_a123 = 0 c_lipo = 0

## Initial conditions # Electrical power Load P_elec = 0

# Start off at full charge Soc_a123 = 1 soc_lipo = 1

v_0_a123 = itp_a123_20C(0) V_O_lipo = discharge_curves_lipo[1][2](0)

kwhr_accum_a123 = 0 kwhr_accum_lipo = 0

ahr_accum_a123 = 0 ahr_accum_lipo = 0

ahr_accum_cell_a123 = ahr_accum_a123/num_cols_a123 ahr_accum_cell_lipo = ahr_accum_lipo/num_cols_lipo

kineticEnergy = 0 height = 0 velocity = sqrt(2 * kineticEnergy / airplaneMass)

localhost:8888/notebooks/SENIOR DESIGN SIMULATION ALL/11/11_9/Hybrid battery analysis Final.ipynb

9/20

2021/11/15 EF1:46

Hybrid battery analysis Final - Jupyter Notebook

v_instantaneous_a123 = v_0_a123 v_instantaneous_lipo = v_e_lipo

voltage_a123_pack = v_instantaneous_a123 * num_rows_a123 voltage_lipo_pack = (v_instantaneous_lipo * num_rows_lipo) - V_drop_diode

if abs(voltage_lipo_pack - voltage_a123_pack) <= .001

V_system = voltage_a123_pack else

V_system = max(voltage_a123_pack, voltage_lipo_pack ) end

I_a123 = 0 I_lipo = 0

# Low-pass variable for changing the power load alpha = 0.05 P_setpoint = 0

# Run the simulation for i=1:(2000/delt)

t = t + delt

if 1==

# Reduce power according to battery limitations if c_lipo > c_lipo_max

P_elec = P_elec - 1000 end else

# Reduce power according to schedule and/or battery limitations if (t<0.1)

P_setpoint = 0 elseif (t<=60)

P_setpoint = P_TAKEOFF elseif (t > 60) && P_setpoint == P_TAKEOFF

P_setpoint = P_MAX_CONTINUOUS elseif (t > 180) && P_setpoint == P_MAX_CONTINUOUS

P_setpoint = P_SUSTAIN_CLIMB elseif (t > 300) && P_setpoint == P_SUSTAIN_CLIMB

P_setpoint = P_SUSTAIN end

P_elec = P_elec + alpha* (P_setpoint-P_elec) end

# Loop enough times to be sure to converge. Convergence is pretty decent after 15 Loops, if p_elec == 0

I_a123 = 0; I_lipo = 0;

C_a123 = 0; c_lipo = 0;

v_instantaneous_a123 = instantaneous_pack_voltage(discharge_index_vector_a123, discharg v_instantaneous_lipo = instantaneous_pack_voltage (discharge_index_vector_a123, discharg

# Saturate battery voltages if v_instantaneous_lipo > 4.2

v_instantaneous_lipo = 4.2

end

localhost:8888/notebooks/SENIOR DESIGN SIMULATION ALL/11/11_9/Hybrid battery analysis Final.ipynb

10/20

2021/11/15 EF1:46

Hybrid battery analysis Final - Jupyter Notebook

if v_instantaneous_a123 > 3.4

v_instantaneous_a123 = 3.4 end

voltage_a123_pack = v_instantaneous_a123 * num_rows_a123 voltage_lipo_pack = (v_instantaneous_lipo * num_rows_lipo) - v_drop_diode

P_split_pct = 0.5; else

# Initialize some variables before going into the convergence Loop loopCount = 1 P_split_pct = 0 seekScalar = .5 lastRoundLipoHigh = true

voltage_a123_pack = v_@_a123 * num_rows_a123 voltage_lipo_pack = (v_0_lipo * num_rows_lipo) - v_drop_diode

while (loopCount < 100 && abs(v_instantaneous_a123-v_instantaneous_lipo) >= 0.001 )

I_a123 = (P_elec * (1-P_split_pct)) / voltage_a123_pack I_lipo = (P_elec * P_split_pct) / voltage_lipo_pack

# Calculate cell discharge rate c_a123 = I_a123 , ahr_a123_pack c_lipo = I_lipo , ahr_lipo_pack

## Determine A123 cell voltages v_instantaneous_a123 = instantaneous_pack_voltage (discharge_index_vector_a123, discha

## Determine LiPo cell voltages v_instantaneous_lipo = instantaneous_pack_voltage (discharge_index_vector_lipo, discha

# Saturate battery voltages if v_instantaneous_lipo > 4.2

v_instantaneous_lipo = 4.2 end

if v_instantaneous_a123 > 3.4

v_instantaneous_a123 = 3.4 end

# Determine pack voltages. This is just the number of batteries in series times the v voltage_a123_pack = v_instantaneous_a123 * num_rows_a123 voltage_lipo_pack = (v_instantaneous_lipo * num_rows_lipo) - v_drop_diode

# Nonlinear search pattern. We're looking for the percentage power split which brings if voltage_lipo_pack > voltage_a123_pack

if (lastRoundLipoHigh == false)

seekScalar = seekScalar/2

end

P_split_pct = P_split_pct + seekScalar

lastRoundLipoHigh = true else

if (lastRoundLipoHigh == true)

seekScalar = seekScalar/2 end

P_split_pct = P_split_pct - seekScalar

localhost:8888/notebooks/SENIOR DESIGN SIMULATION ALL/11/11_9/Hybrid battery analysis Final.ipynb

11/20

2021/11/15 EF1:46

Hybrid battery analysis Final - Jupyter Notebook

lastRoundLipoHigh = false end

if p_split_pct > 1

P_split_pct =1 elseif p_split_pct < 0

P_split_pct = 0 end

# Increment loop variables.

loopCount = loopCount + 1 end

# Check if voltages successfully converged. Do this check only when there is power bein if abs(voltage_lipo_pack - voltage_a123_pack) > 0.1 && c_lipo > 0.1 && c_a123 > 0.1

println("Voltages did not converge at t=" * string(round(t, digits = 2)) * ", voltage

break; end

end

# Update the system voltage if abs(voltage_lipo_pack - voltage_a123_pack) <= .001

V_system = voltage_a123_pack else

# This is the case where the A123Systems pack hasn't discharged down to the Lipo/Li-ion

V_system = max(voltage_a123_pack, voltage_lipo_pack ) end

# Calculate accumulated amp-hour consumption ahr_accum_a123 = ahr_accum_a123 + I_a123 * delt/3600 ahr_accum_lipo = ahr_accum_lipo + I_lipo * delt/3600

# Calculate accumulated discharge from individual cells ahr_accum_cell_a123 = ahr_accum_a123/num_cols_a123 ahr_accum_cell_lipo = ahr_accum_lipo/num_cols_lipo

# Calculate instantaneous power P_instantaneous_a123 = I_a123 * V_system P_instantaneous_lipo = I_lipo * V_system

# Calculate accumulated kw-hour consumption kwhr_accum_a123 = kwhr_accum_a123 + P_instantaneous_a123 * delT/3600/1000 kwhr_accum_lipo = kwhr_accum_lipo + p_instantaneous_lipo * delt/3600/1000

# Calculate State of Charge soc_a123 = 1 - ahr_accum_a123/ahr_a123_pack soc_lipo = 1 - ahr_accum_lipo/ahr_lipo_pack

# Stop the experiment if a pack is dead if (ahr_accum_a123 > ahr_a123_pack && (num_cols_a123 * num_rows_a123 > 0)) || ahr_accum_1

println("[BATTERY EMPTY] t: " * string(round(t, digits = 1)) * ", A123: " * string(ro break

end

# Mark the point in time when the A123Systems pack's SoC goes below 5% if soc_5_a123 == 0 && soc_a123 < 0.05

soc_5_a123 = t end

# Mark the point in time when the Lipo/Li-ion pack's SoC goes below 20%

localhost:8888/notebooks/SENIOR DESIGN SIMULATION ALL/11/11_9/Hybrid battery analysis Final.ipynb

12/20

2021/11/15 EF1:46

Hybrid battery analysis Final - Jupyter Notebook if soc_20_lipo == 0 && soc_lipo < 0.20

soc_20_lipo = t end

# End the simulation one minute after the Lipo/Li-ion if soc_20_lipo !=0 && (t-soc_20_lipo) > 60

break end

# Simulate airplane. This is an extremely simplified model, but it works fine for these p drag = airplaneMass * 9.805/glide Ratio * (velocity/climbVelocity)^2 if (velocity < climbVelocity)

# Below climbVelocity, we haevn't taken off yet eff = .4 kineticEnergy = kineticEnergy + (P_elec * eff - velocity * drag) * delt velocity = sqrt(2 * kineticEnergy / airplaneMass)

h_dot = 0 else

# Above climbVelocity, we're putting excess energy into climbing eff = .8*.90 # Propller efficiency times electrical efficiency h_dot = (P_elec * eff - velocity * drag)/(airplaneMass*9.805) height = height + h_dot*delt end

# Some useful console spew if 1==0

println(

t, ": ",

" [",

round(v_instantaneous_a123, digits=3), " ", round(voltage_a123_pack, digits=2), " ", round(C_a123, digits=1), ",", round(ahr_accum_a123, digits=4), ",", round(soc_a123*100, digits=1), "], [", round(v_instantaneous_lipo, digits=3), "" round(voltage_lipo_pack, digits=2), ", ", round(c_lipo, digits=1), ", ", round(ahr_accum_lipo, digits=4), ",",

round(soc_lipo*100, digits=1), "], :", round(voltage_a123_pack*I_a123 + voltage_lipo_pack*I_lipo)) end

append!(t_experiment, t) append! (c_a123_experiment, c_a123) append! (c_lipo_experiment, c_lipo) append! (soc_a123_experiment, soc_a123) append! (soc_lipo_experiment, soc_lipo) append! (V_a123, voltage_a123_pack) append! (V_lipo, voltage_lipo_pack) append! (V_bus, V_system) append! (P_experiment, P_elec) append! (P_a123, p_instantaneous_a123) append! (P_lipo, p_instantaneous_lipo) append! (E_a123, kwhr_accum_a123) append! (E_lipo, kwhr_accum_lipo) append!(vel_airplane, velocity)

localhost:8888/notebooks/SENIOR DESIGN SIMULATION ALL/11/11_9/Hybrid battery analysis Final.ipynb

13/20

Hybrid battery analysis Final - Jupyter Notebook

2021/11/15 E41:46

append! (hgt_airplane, height) append! (hgt_dot_airplane, h_dot)

end

[soc_5_a123, soc_20_lipo]

Out[2157]:

2-element Vector{Float64}:

115.2499999999956 633,7499999999714

In [2158]: plot(t_experiment, P_experiment./1000, xlabel = "Time", ylabel = "kw", ylims=[0, Inf], title

plot!(t_experiment, [P_a123 P_lipo]./1000, label=[pack_A_label pack_B_label])

hline! ([P_TAKEOFF, P_MAX_CONTINUOUS, P_SUSTAIN_CLIMB, P_SUSTAIN]./1000, lw=0.5, label="") vline!([60, soc_5_a123, soc_20_lipo], lw=0.5, label="")

Out[2158]:

Input electrical power A123 LiFePo4 (19S1P)/Li-ion (125, 10P,42.0Ahr)

Total power A123 LiFePo4 (19S1P) - Li-ion (129, 10P,42.0Ahr)

MY

u

200

400

600

Time

localhost:8888/notebooks/SENIOR DESIGN SIMULATION ALL/11/11_9/Hybrid battery analysis Final.ipynb

14/20

2021/11/15 EF1:46

Hybrid battery analysis Final - Jupyter Notebook

In [2159]:

colorRightAxis = [:blue :red] linestyleRightAxis = :solid

plot(t_experiment, [V_bus], xlabel = "Time", title=("Pack voltage\n [Nominal] LiFePO4: " * $

# Plot the times when the packs are empty vline!([soc_5_a123, soc_20_lipo], lw=0.5, label="")
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

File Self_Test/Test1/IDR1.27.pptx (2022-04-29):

## IDR Senior Design 2

Team Lead: Steven Wang

## Deliverables

- Test 1 Design
  - Test 1 Schematic
- FMEA
  - Design Correction
- Test design timeline
- BOM
  - Purchase Parts

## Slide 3

Test 1 Schematic

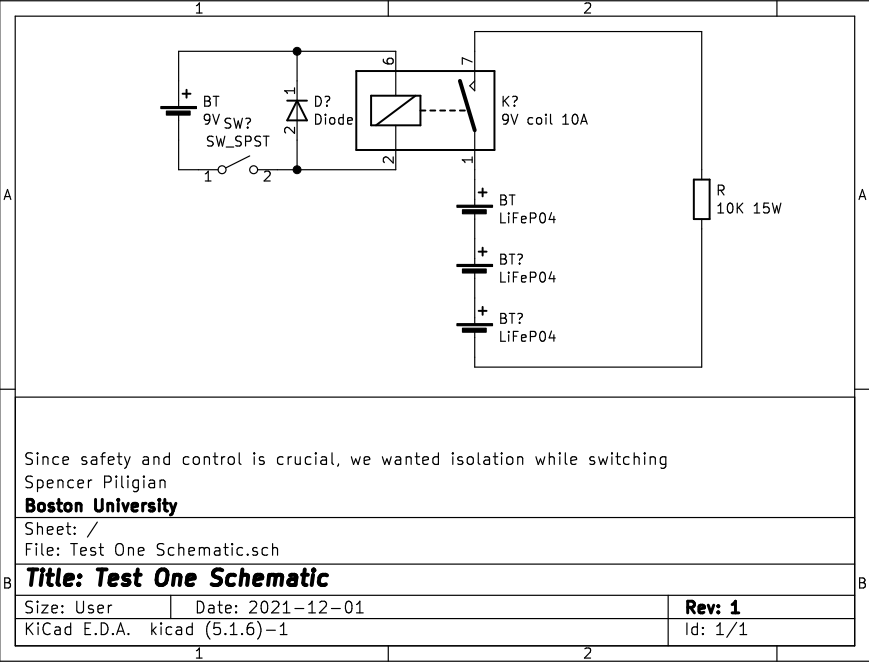
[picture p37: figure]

## FMEA

Failures | Severity | Occurrence | Detection | RPN | Correction
Short in Ckt | 9 | 3 | 1 | 27 | Fuse Relay
Overloading wires | 8 | 1 | 5 | 40 | Good wire ratings
Bad battery connection | 4 | 7 | 1 | 28 | Reliable battery holder Good terminals
Overheating | 6 | 4 | 1 | 24 | Live temp. sensor
Switch failure | 2 | 1 | 1 | 2 | N/A
Environmental | 3 | 1 | 1 | 3 | N/A

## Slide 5

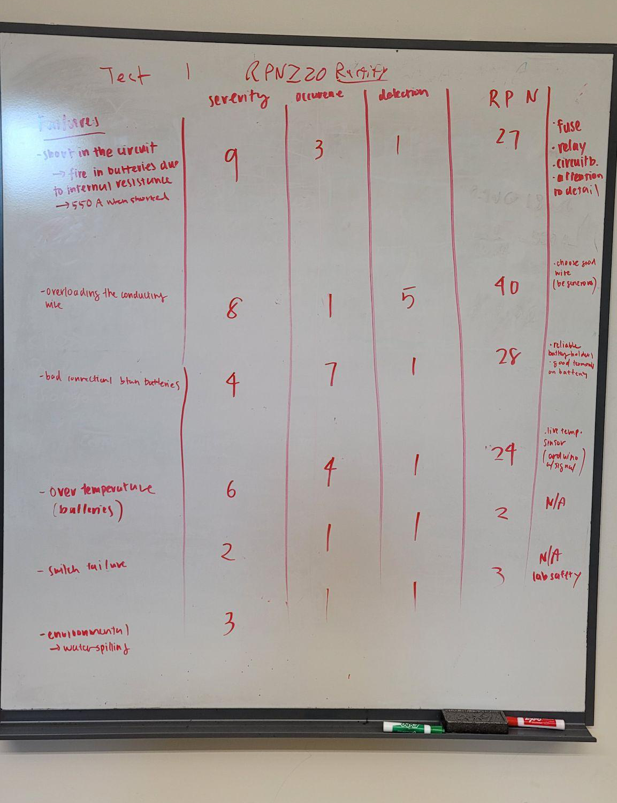
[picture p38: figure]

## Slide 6

FMEA Design Correction

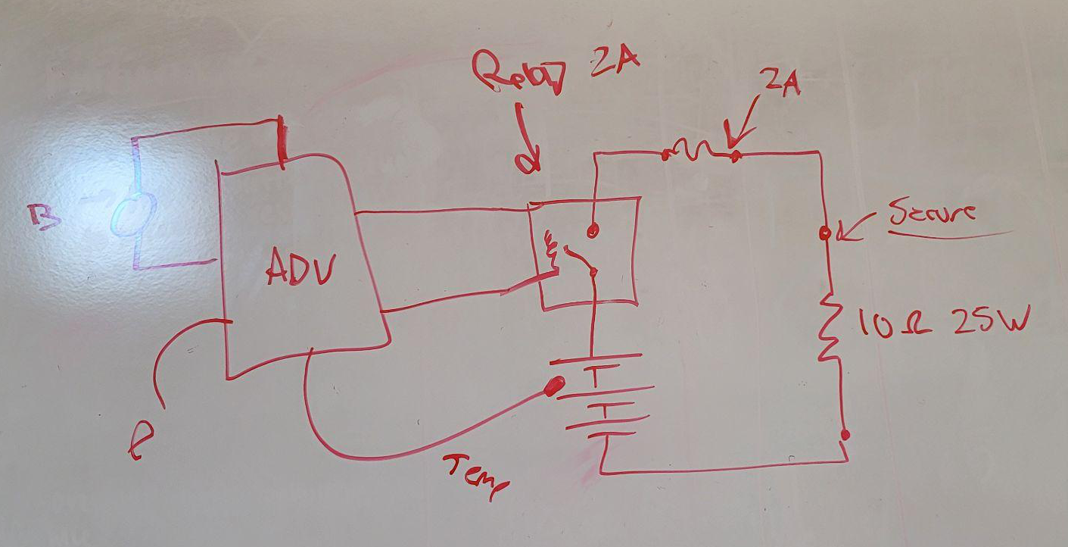
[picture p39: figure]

## Timeline

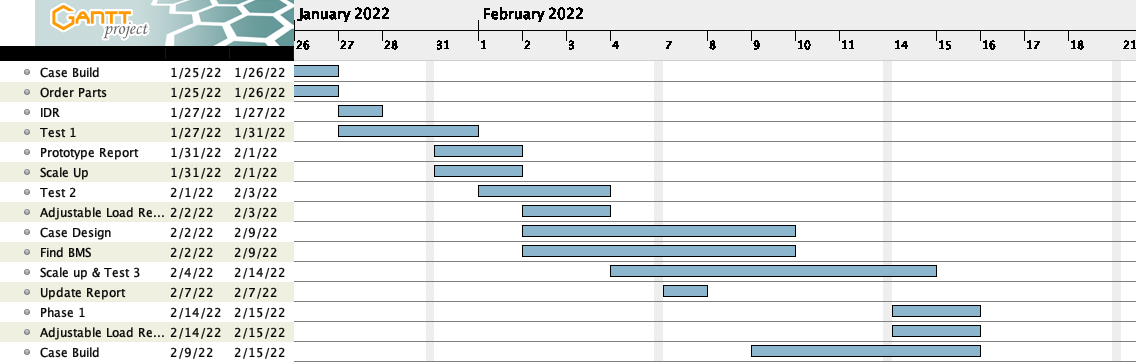
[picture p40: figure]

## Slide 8

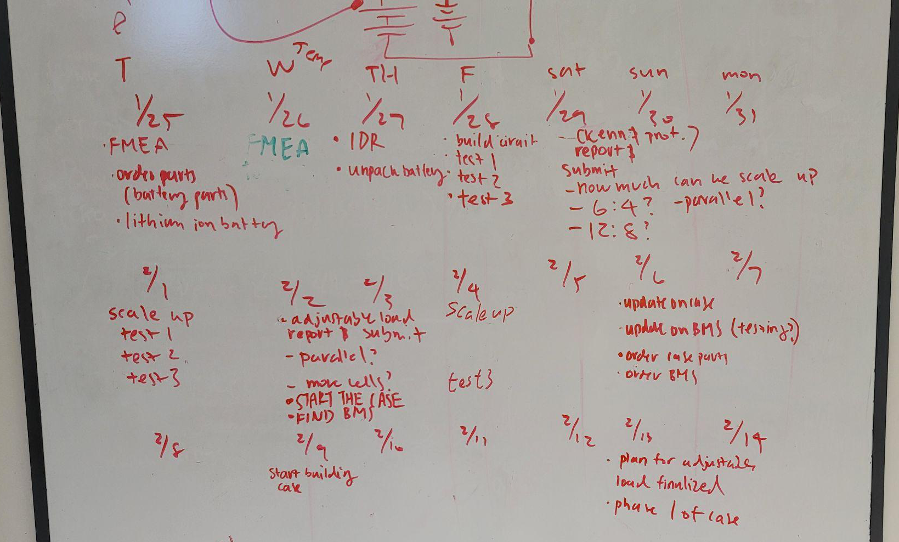
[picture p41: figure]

## Bill of Materials (Test 1)

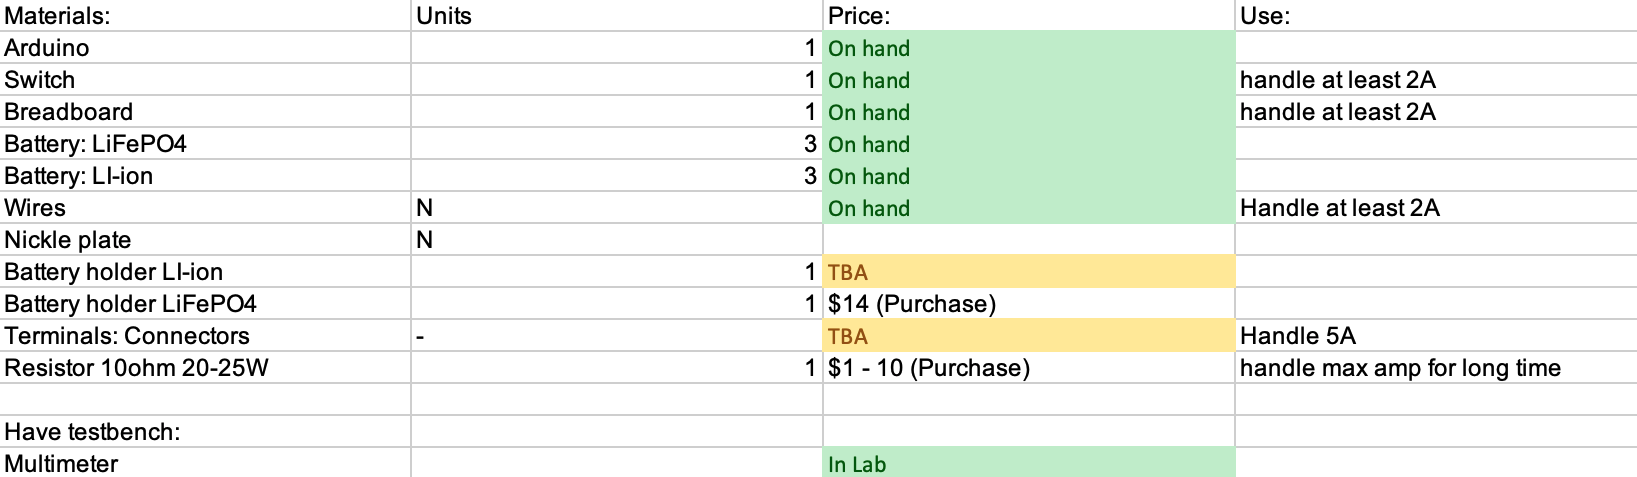
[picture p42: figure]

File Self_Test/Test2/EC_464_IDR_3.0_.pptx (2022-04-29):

## ECE 464: Senior Design 2 IDR 3.0

Team Lead: Steven Wang

## Deliverables 3

- Design 2 Test
  - Results
- Scale up
- Project Design timeline
- Purchase Parts
    - BMS
    - Batteries
    - Speed Controller

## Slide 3

Test 2 Schematic


## Test 2 Results

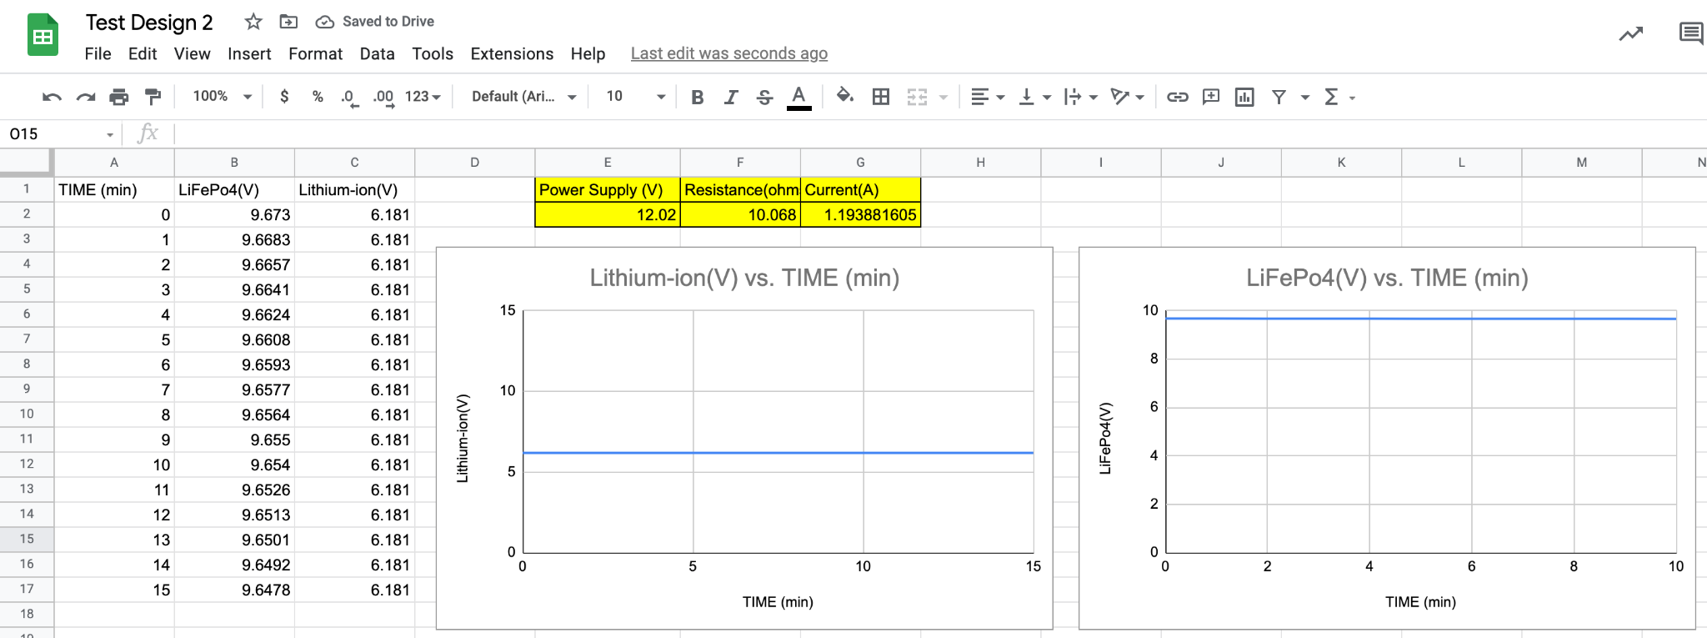
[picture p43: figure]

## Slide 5

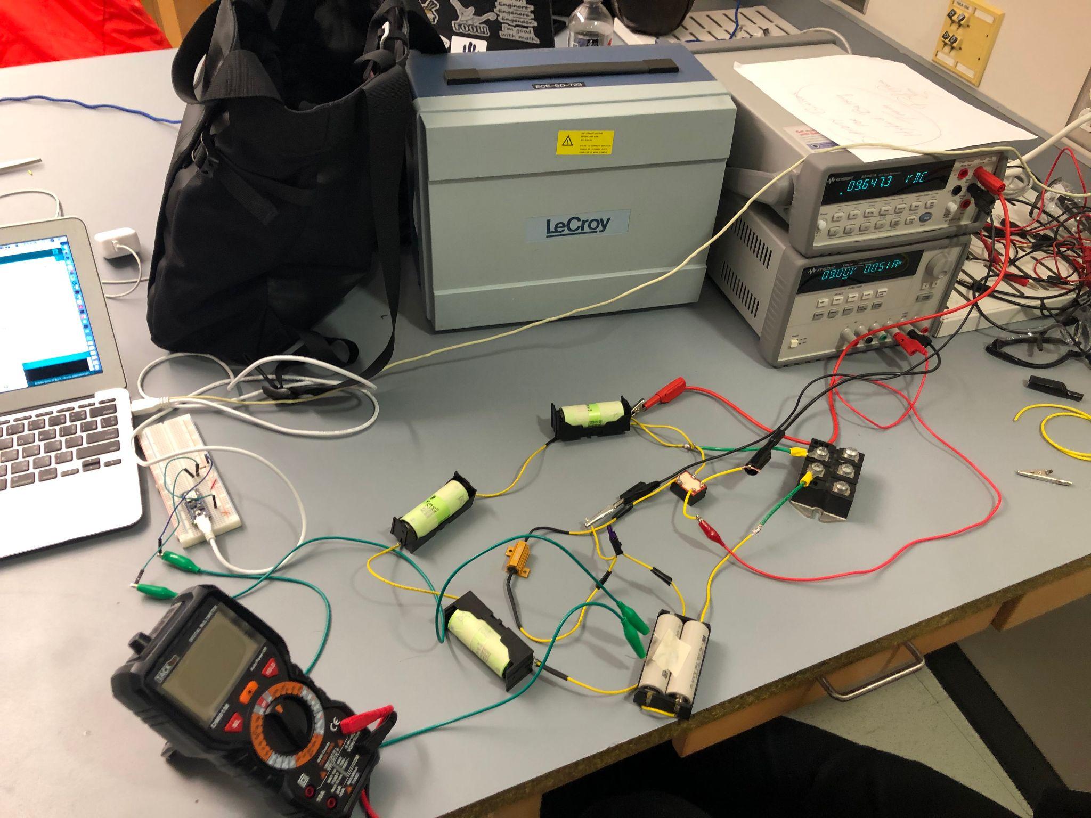
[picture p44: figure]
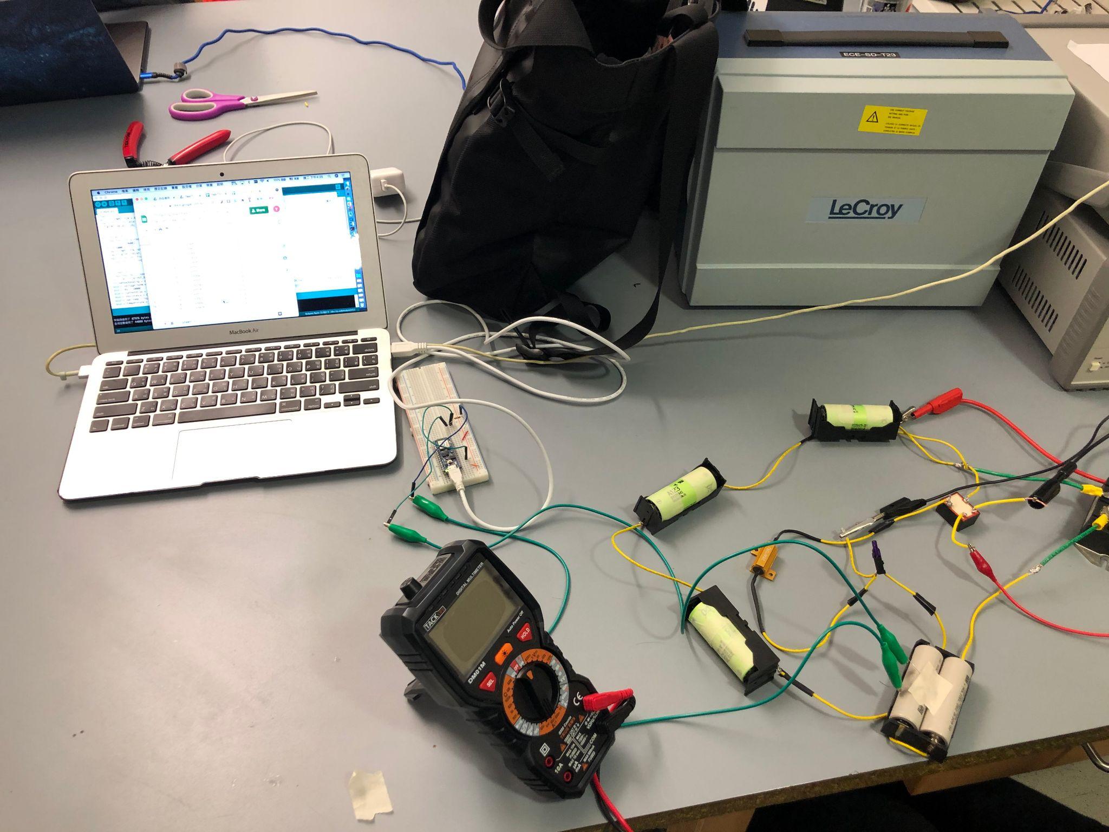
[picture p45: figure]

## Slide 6

Purchase

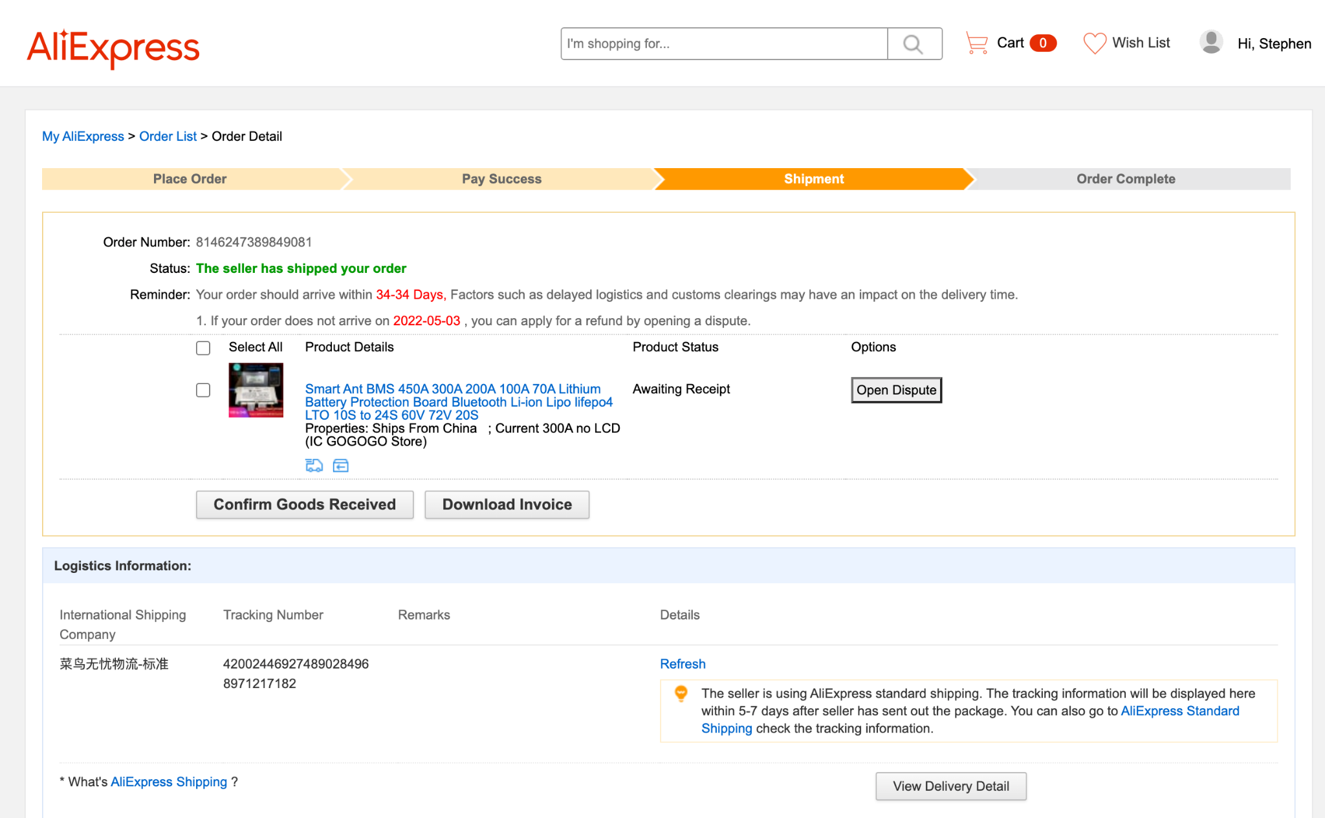
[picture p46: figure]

Item | Amount | Cost
LiFePo4 | 48 | 65.09
Li-ion | 2 | 28.54
Battery holder | 1 | 14.44
~~Flipsky Speed Controller~~ | ~~2~~ | ~~300~~
24S LiFePo4 BMS | 1 | 99.89
Total | 207.96

## Timeline


## Extra previous IDR

## Deliverables 1

- Test 1 Design
- FMEA
  - Design Correction
- Test design timeline
- BOM
  - Purchase Parts

## Deliverables 2

- Design 1 Test
  - Results
- Test design timeline
- BOM
  - Purchase Parts
    - BMS
    - Batteries
    - Power Supplies

## Test 1 Results


- 88 Data points
- 1 hr 30 mins

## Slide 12


## Objectives 2.10 - 2.17

- Scale up
- Design 2
  - Design 2 Test
- Others:
  - Adjustable load
  - Battery
  - BMS
  - Case design

## FMEA

Failures | Severity | Occurrence | Detection | RPN | Correction
Short in Ckt | 9 | 3 | 1 | 27 | Fuse Relay
Overloading wires | 8 | 1 | 5 | 40 | Good wire ratings
Bad battery connection | 4 | 7 | 1 | 28 | Reliable battery holder Good terminals
Overheating | 6 | 4 | 1 | 24 | Live temp. sensor
Switch failure | 2 | 1 | 1 | 2 | N/A
Environmental | 3 | 1 | 1 | 3 | N/A

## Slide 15


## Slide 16

FMEA Design Correction


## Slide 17


## Bill of Materials (Test 1)


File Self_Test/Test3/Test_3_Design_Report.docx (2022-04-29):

Hybrid Battery Pack Test #3 Preliminary Design Report

EC464 Team #23

Spring 2022

Hybrid Battery Pack Schematic

Expounding upon the expected successful results from the first two hybrid battery pack safety tests, the third test in this series employs two Lithium-ion batteries and three LiFePo4 batteries in parallel. Adjustments will be made accordingly to the resistive load in order to gain a comprehensive picture of the safety bounds relative to an intermittent resistive demand, hence making the resistor variable accordingly. A schematic of the third test can be found below; this was drawn using KiCad EDA – a free, open-source software commonly used for electronics design and PCB design. Increasing from the first two tests, in this test, a 7A fuse will be added in series with the adjustable resistive load accordingly. This is an expected safety precaution and consequence of scaling up the hybrid battery pack for further test standards. Overtly, for test #3, the team expects to have a circuit configuration with three LiFePo4 batteries in series that are in parallel (3S, 1P) with two Lithium-ion batteries in series (2S, 1P); this configuration has been selected so as to scale up the current to 5 A whilst the voltage is set to 10 V (so 50 W) based on Professor feedback from the IDRs last week. Ultimately, with this test, the team expects that the final product will include 19 LiFePo4 batteries in series (19S, 1P) that are in parallel with 12 Lithium-ion batteries in series and eight in parallel (12S, 8P). On the left side of the schematic below, a VESC motor controller will be used to drive the adjustable resistive load for battery testing.


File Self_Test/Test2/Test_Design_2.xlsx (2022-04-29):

TIME (min) | LiFePo4(V) | Lithium-ion(V) | Power Supply (V) | Resistance(ohms) | Current(A)
0 | 9.673 | 6.181 | 12.02 | 10.068 | 1.193881605
1 | 9.6683 | 6.181
2 | 9.6657 | 6.181
3 | 9.6641 | 6.181
4 | 9.6624 | 6.181
5 | 9.6608 | 6.181
6 | 9.6593 | 6.181
7 | 9.6577 | 6.181
8 | 9.6564 | 6.181
9 | 9.655 | 6.181
10 | 9.654 | 6.181
11 | 9.6526 | 6.181
12 | 9.6513 | 6.181
13 | 9.6501 | 6.181
14 | 9.6492 | 6.181
15 | 9.6478 | 6.181

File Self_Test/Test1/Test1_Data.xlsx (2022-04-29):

Seconds | Mintues | Voltage (V) | Power Supply (V) | Resistance(ohms) | Current(A)
134 | 2.233333333 | 6.9203 | 12.02 | 10.068 | 1.193881605
194 | 3.233333333 | 6.91
254 | 4.233333333 | 6.899
314 | 5.233333333 | 6.887
374 | 6.233333333 | 6.882
434 | 7.233333333 | 6.8725
494 | 8.233333333 | 6.8638
554 | 9.233333333 | 6.854
614 | 10.23333333 | 6.8463
674 | 11.23333333 | 6.8387
734 | 12.23333333 | 6.8313
794 | 13.23333333 | 6.8245
854 | 14.23333333 | 6.8186
914 | 15.23333333 | 6.8134
974 | 16.23333333 | 6.8096
1034 | 17.23333333 | 6.8042
1094 | 18.23333333 | 6.7991
1154 | 19.23333333 | 6.7952
1214 | 20.23333333 | 6.7908
1274 | 21.23333333 | 6.7866
1334 | 22.23333333 | 6.782
1394 | 23.23333333 | 6.777
1454 | 24.23333333 | 6.7725
1514 | 25.23333333 | 6.7684
1574 | 26.23333333 | 6.7613
1634 | 27.23333333 | 6.7592
1694 | 28.23333333 | 6.7546
1754 | 29.23333333 | 6.7486
1814 | 30.23333333 | 6.7432
1874 | 31.23333333 | 6.7383
1934 | 32.23333333 | 6.731
1994 | 33.23333333 | 6.7256
2054 | 34.23333333 | 6.7193
2114 | 35.23333333 | 6.7108
2174 | 36.23333333 | 6.7
2234 | 37.23333333 | 6.686
2294 | 38.23333333 | 6.68218
2354 | 39.23333333 | 6.6695
2414 | 40.23333333 | 6.6538
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

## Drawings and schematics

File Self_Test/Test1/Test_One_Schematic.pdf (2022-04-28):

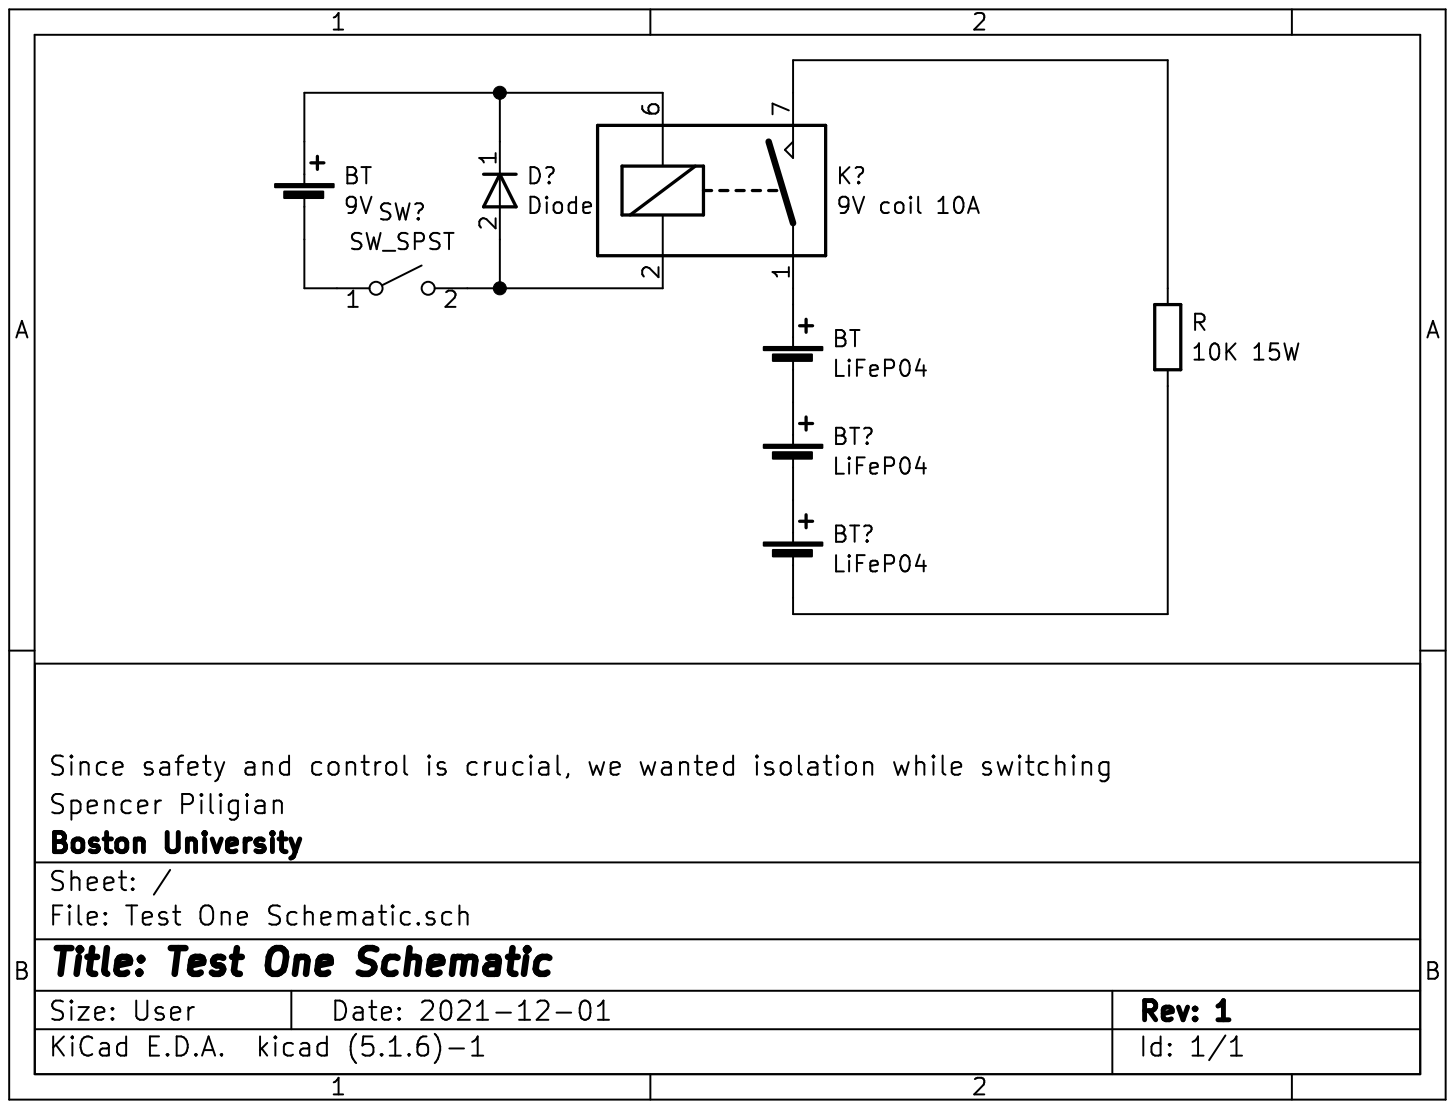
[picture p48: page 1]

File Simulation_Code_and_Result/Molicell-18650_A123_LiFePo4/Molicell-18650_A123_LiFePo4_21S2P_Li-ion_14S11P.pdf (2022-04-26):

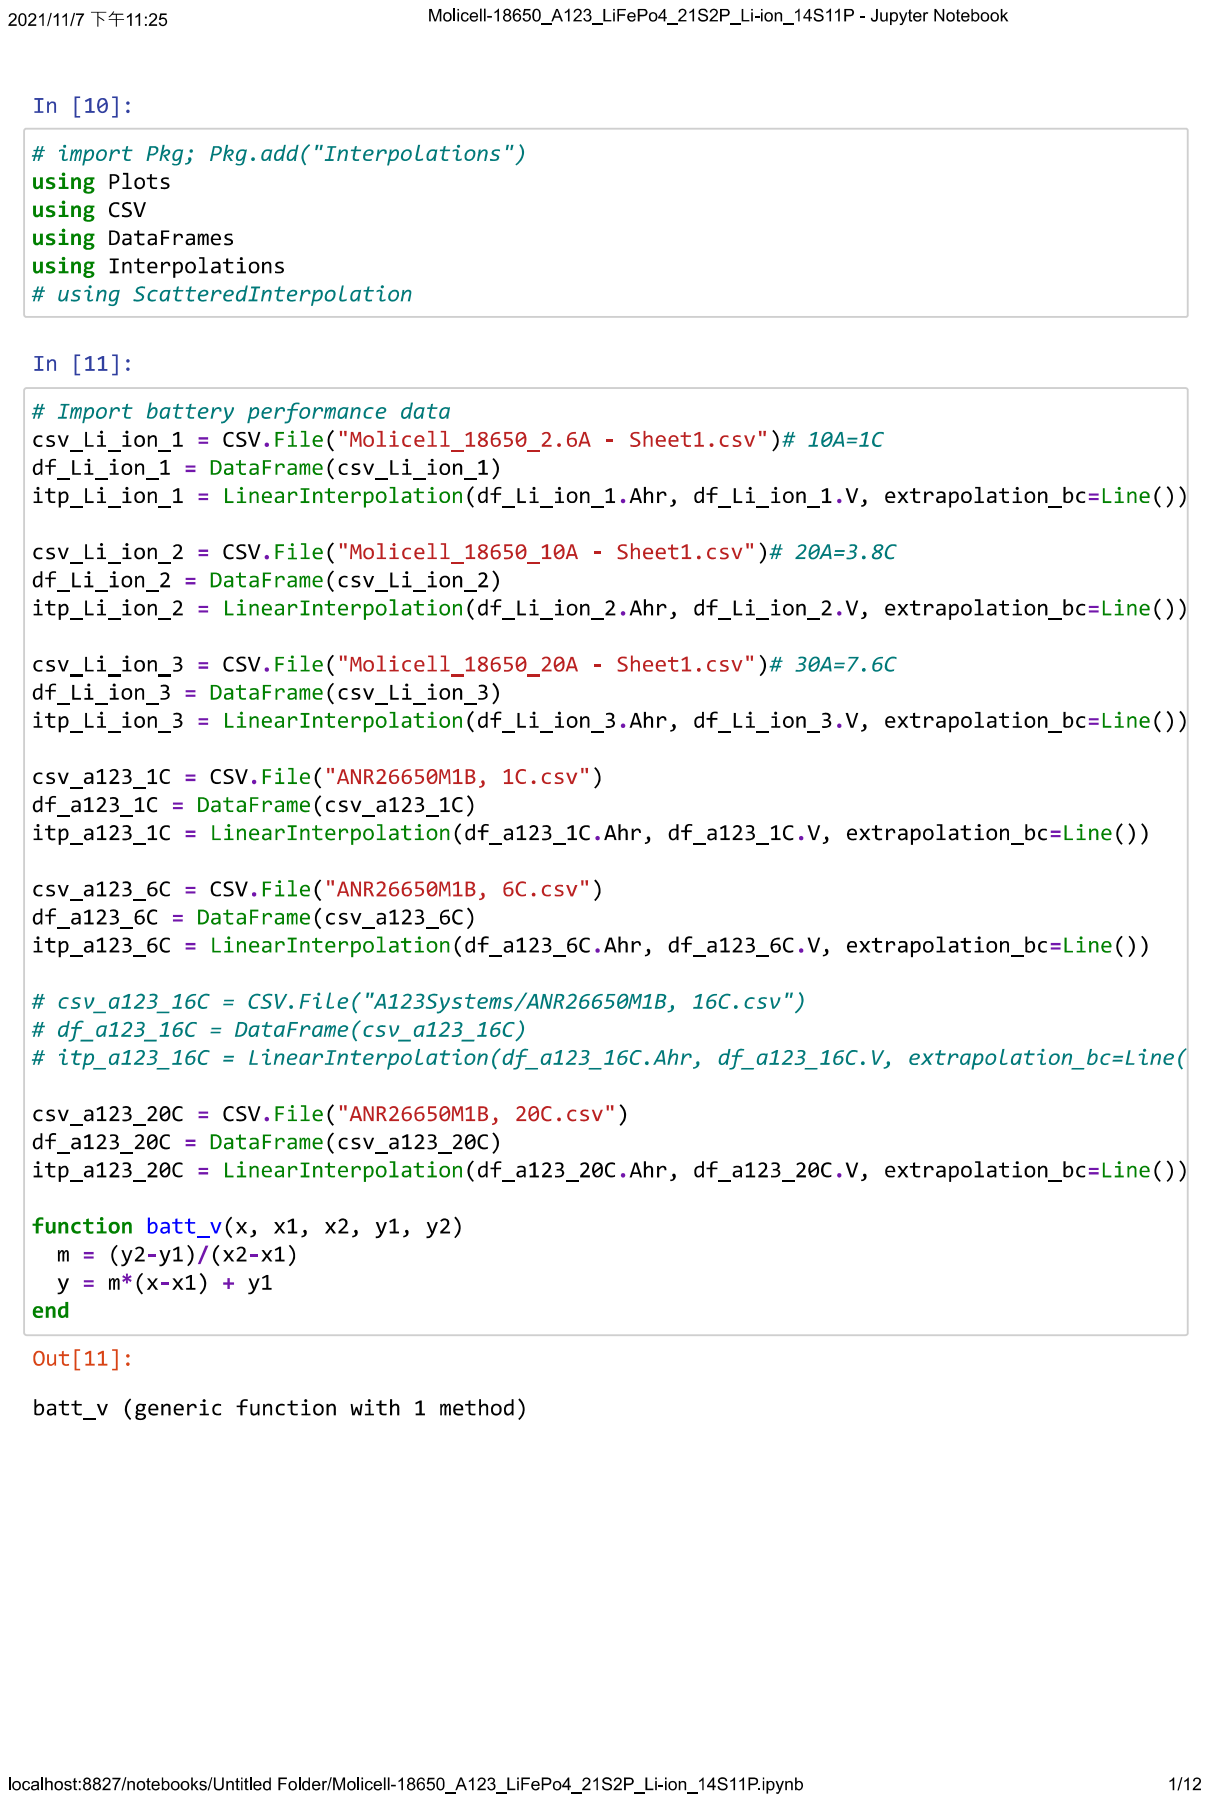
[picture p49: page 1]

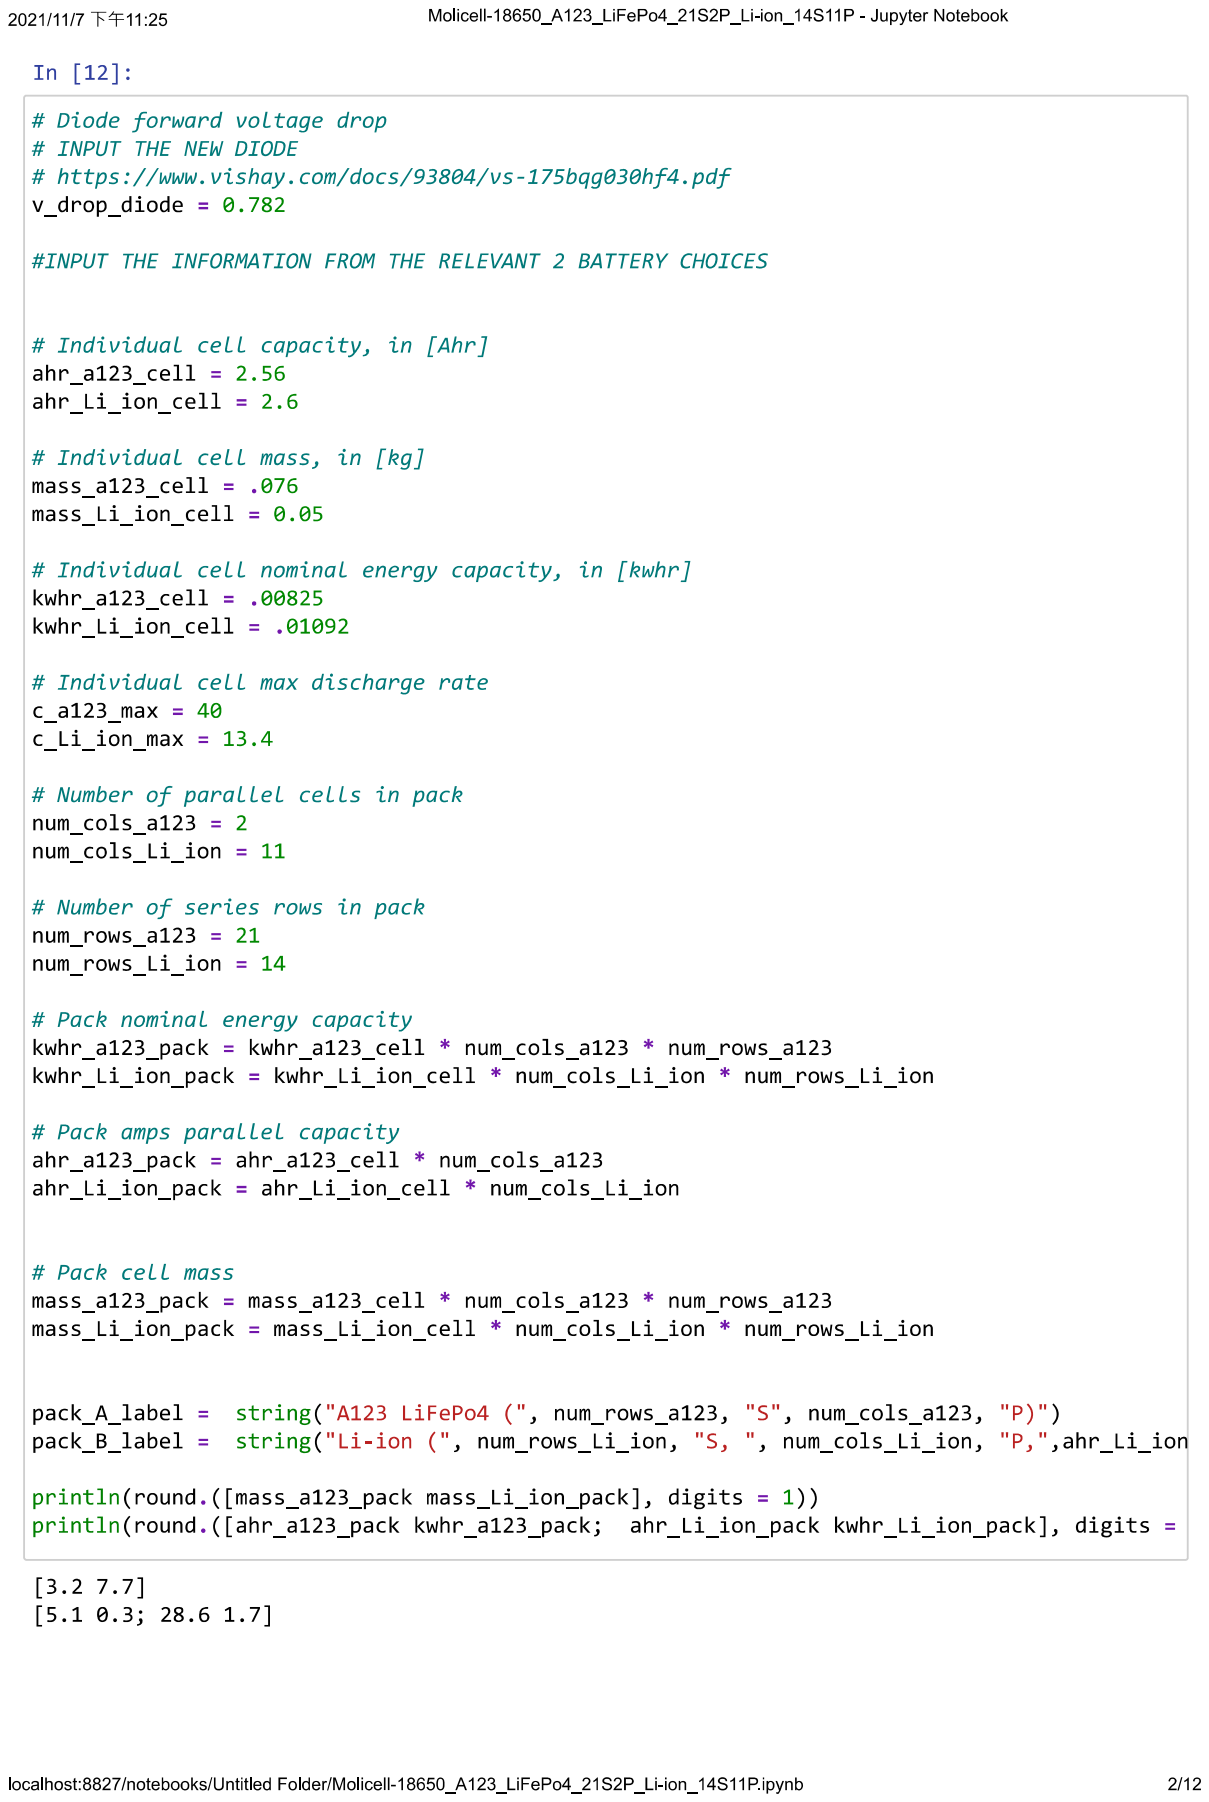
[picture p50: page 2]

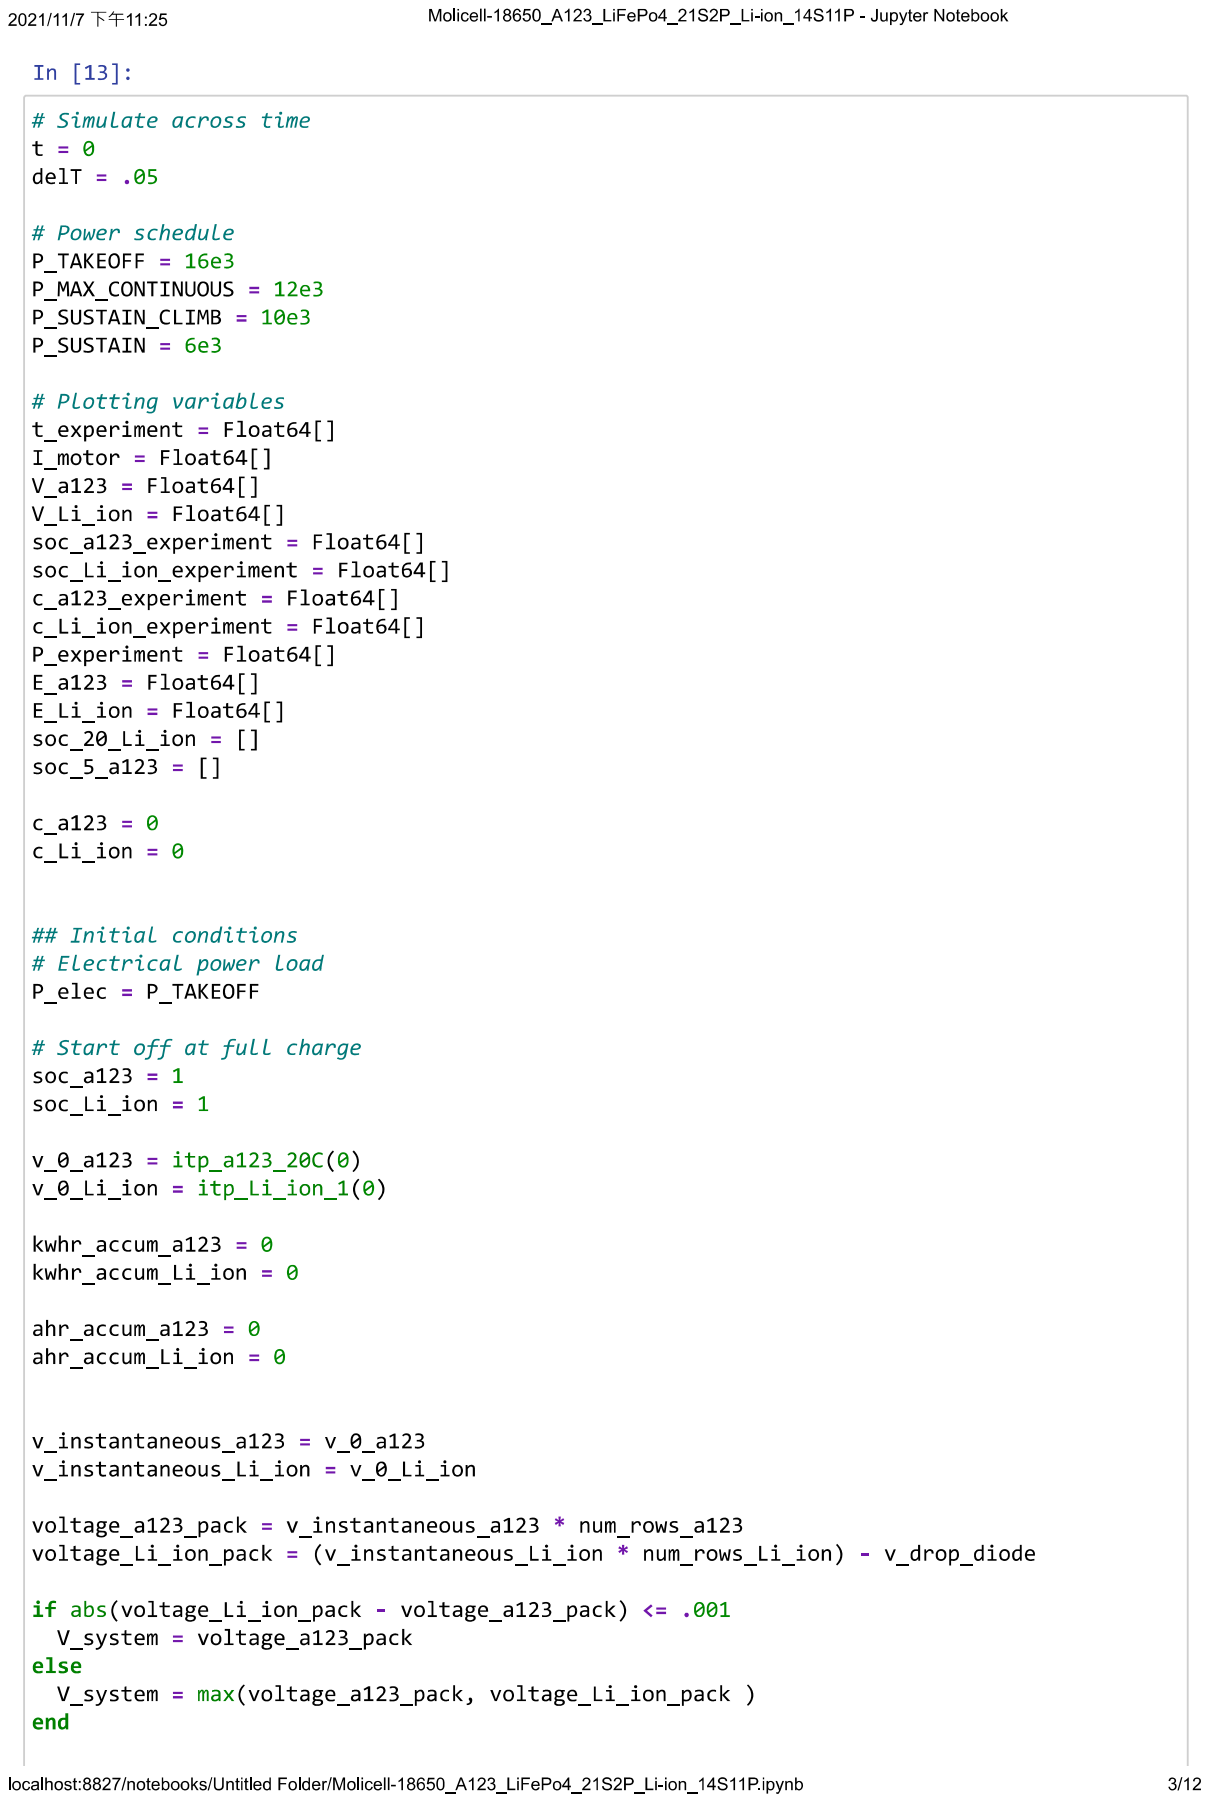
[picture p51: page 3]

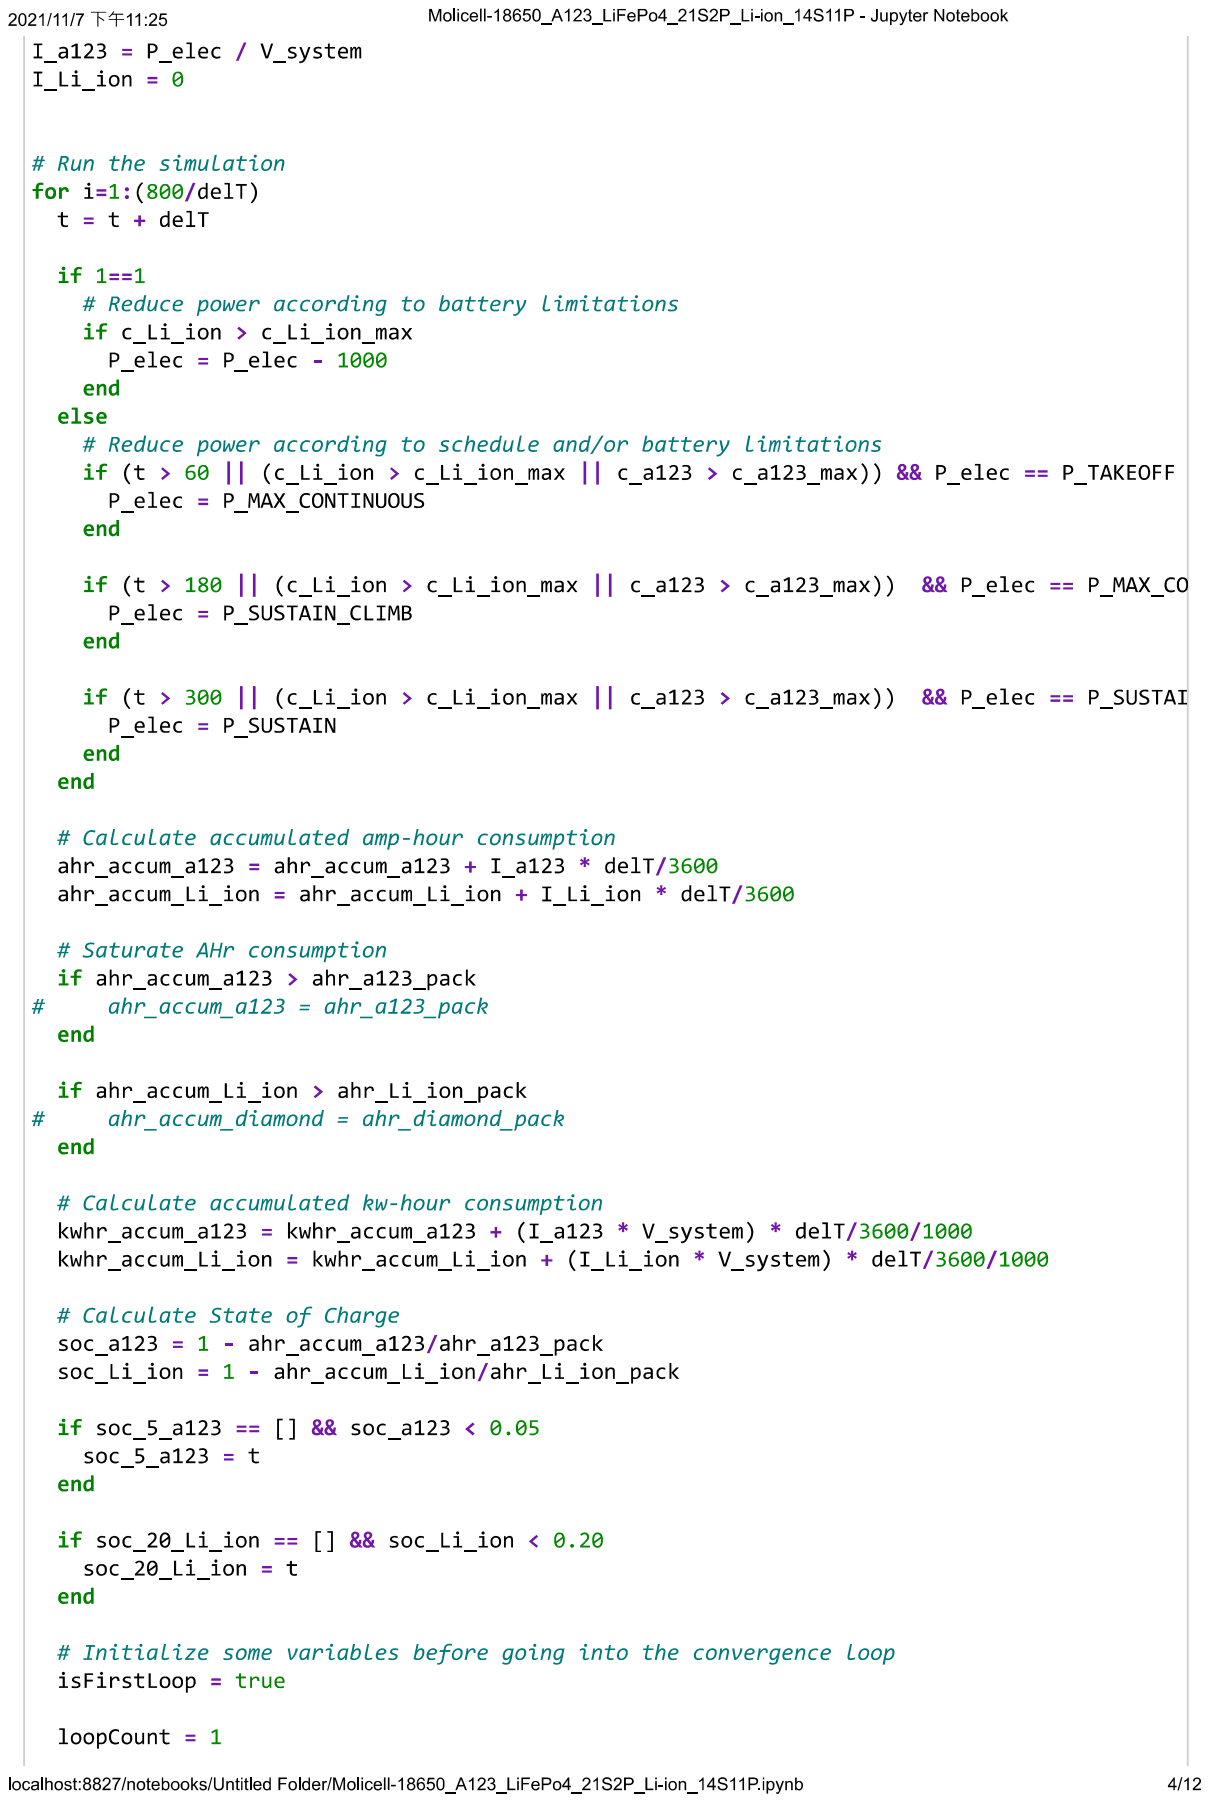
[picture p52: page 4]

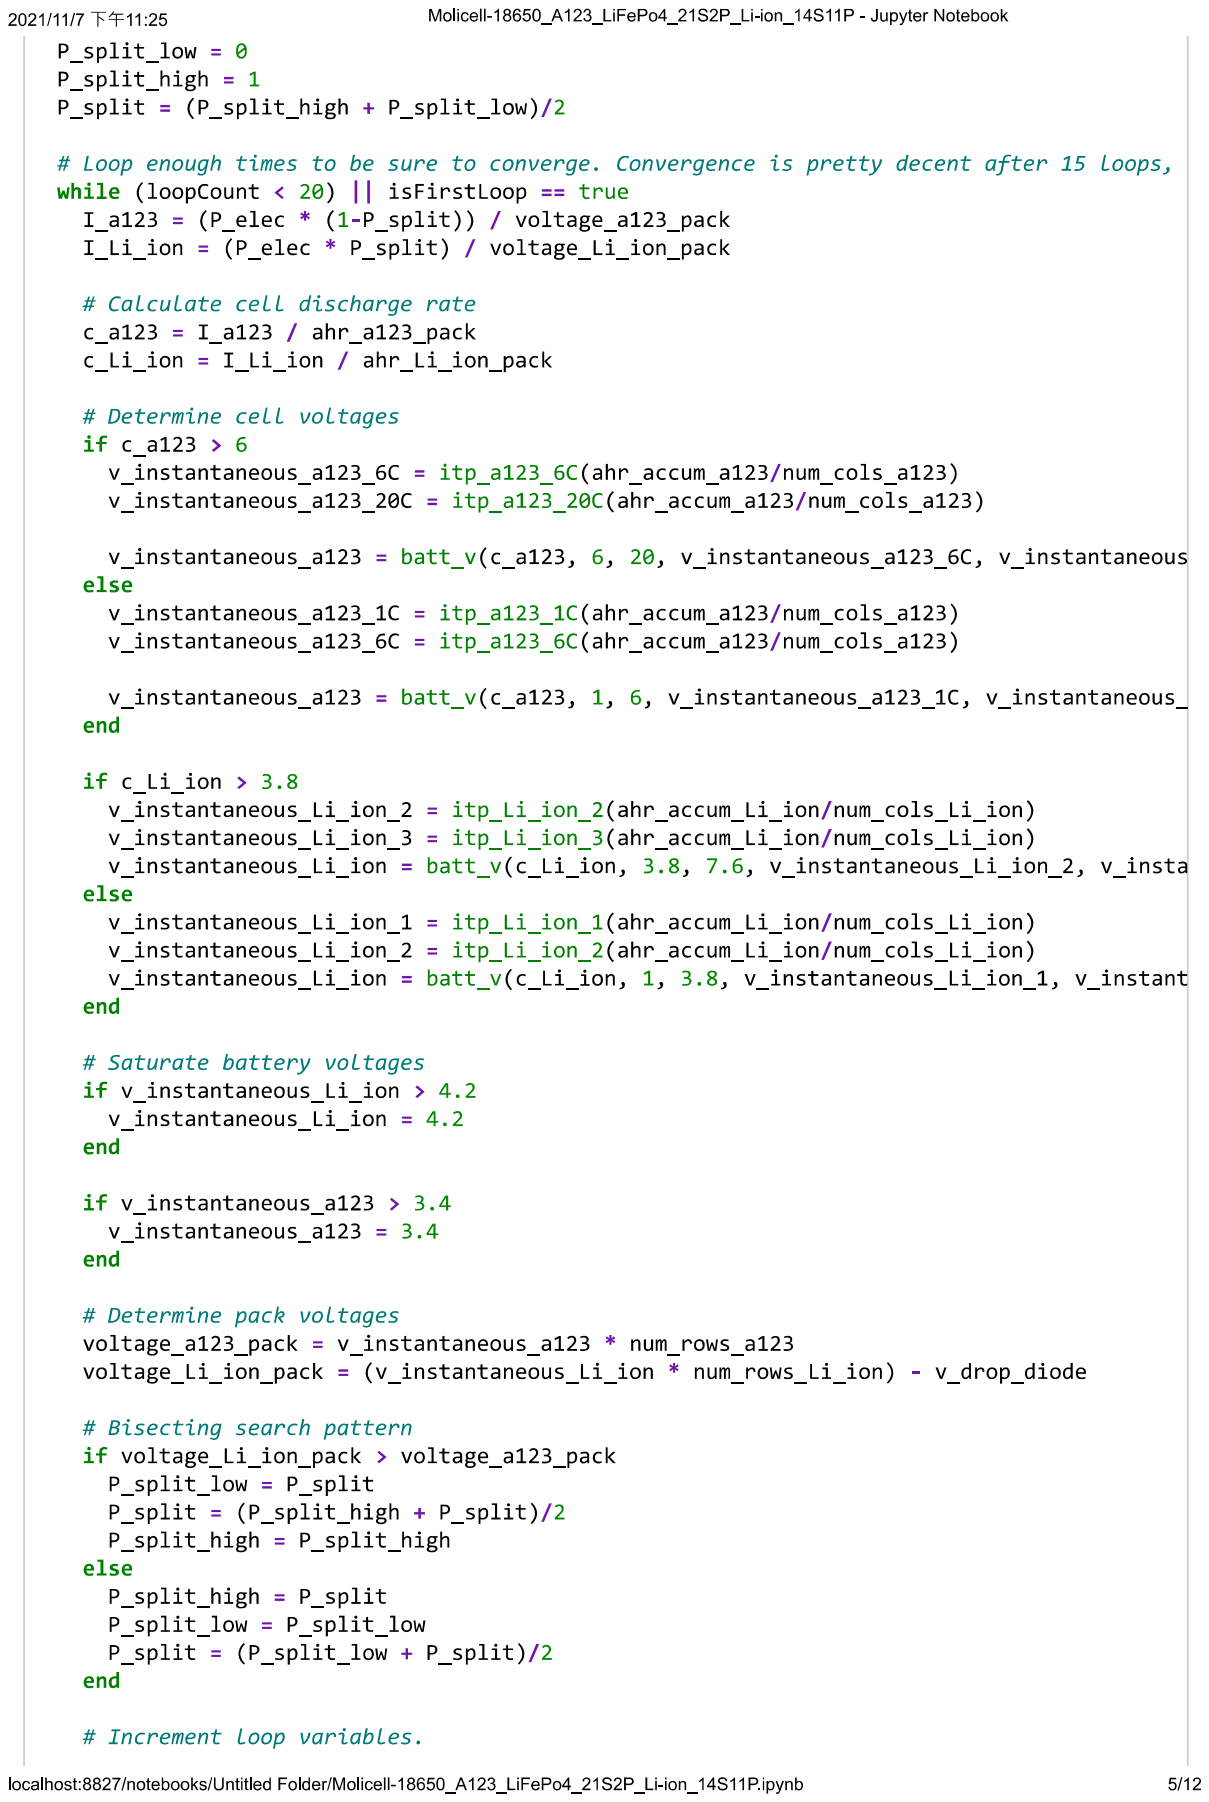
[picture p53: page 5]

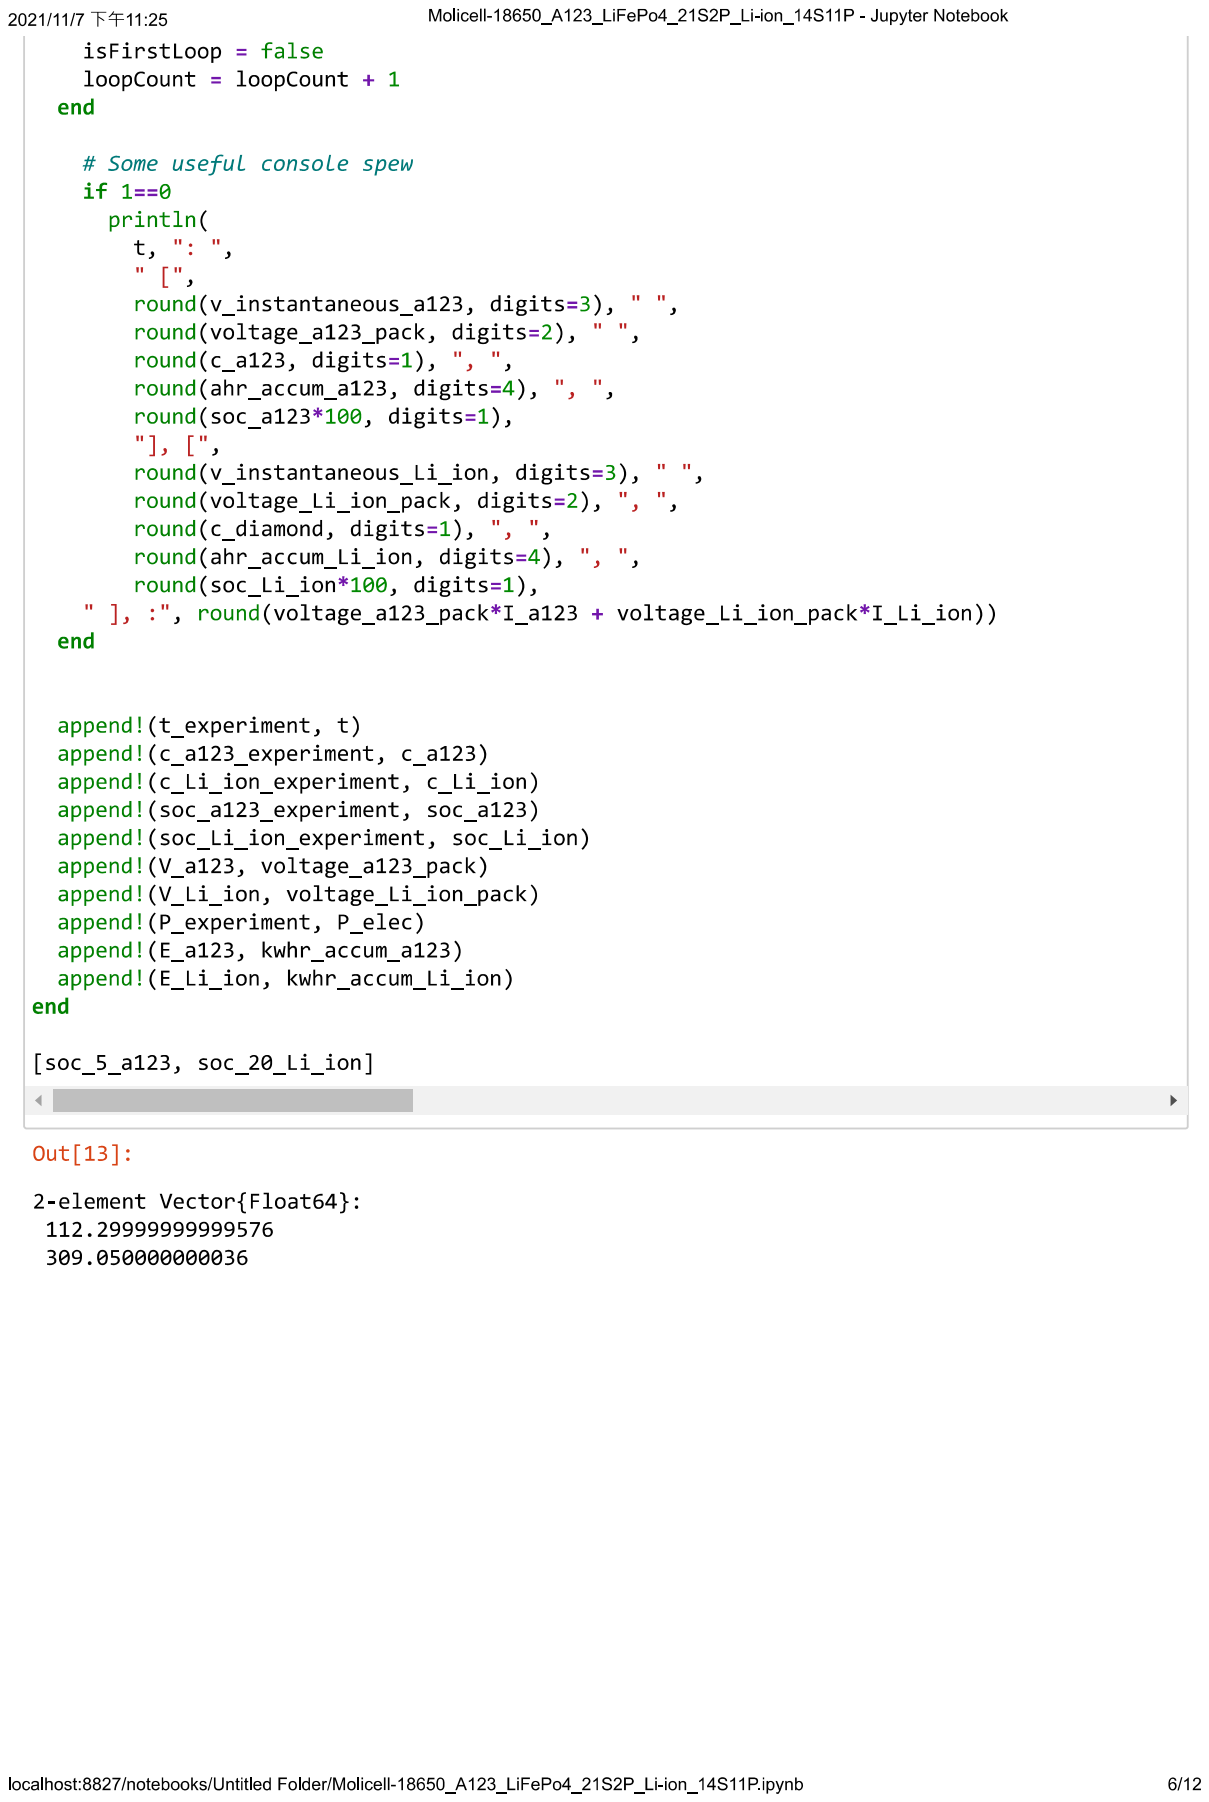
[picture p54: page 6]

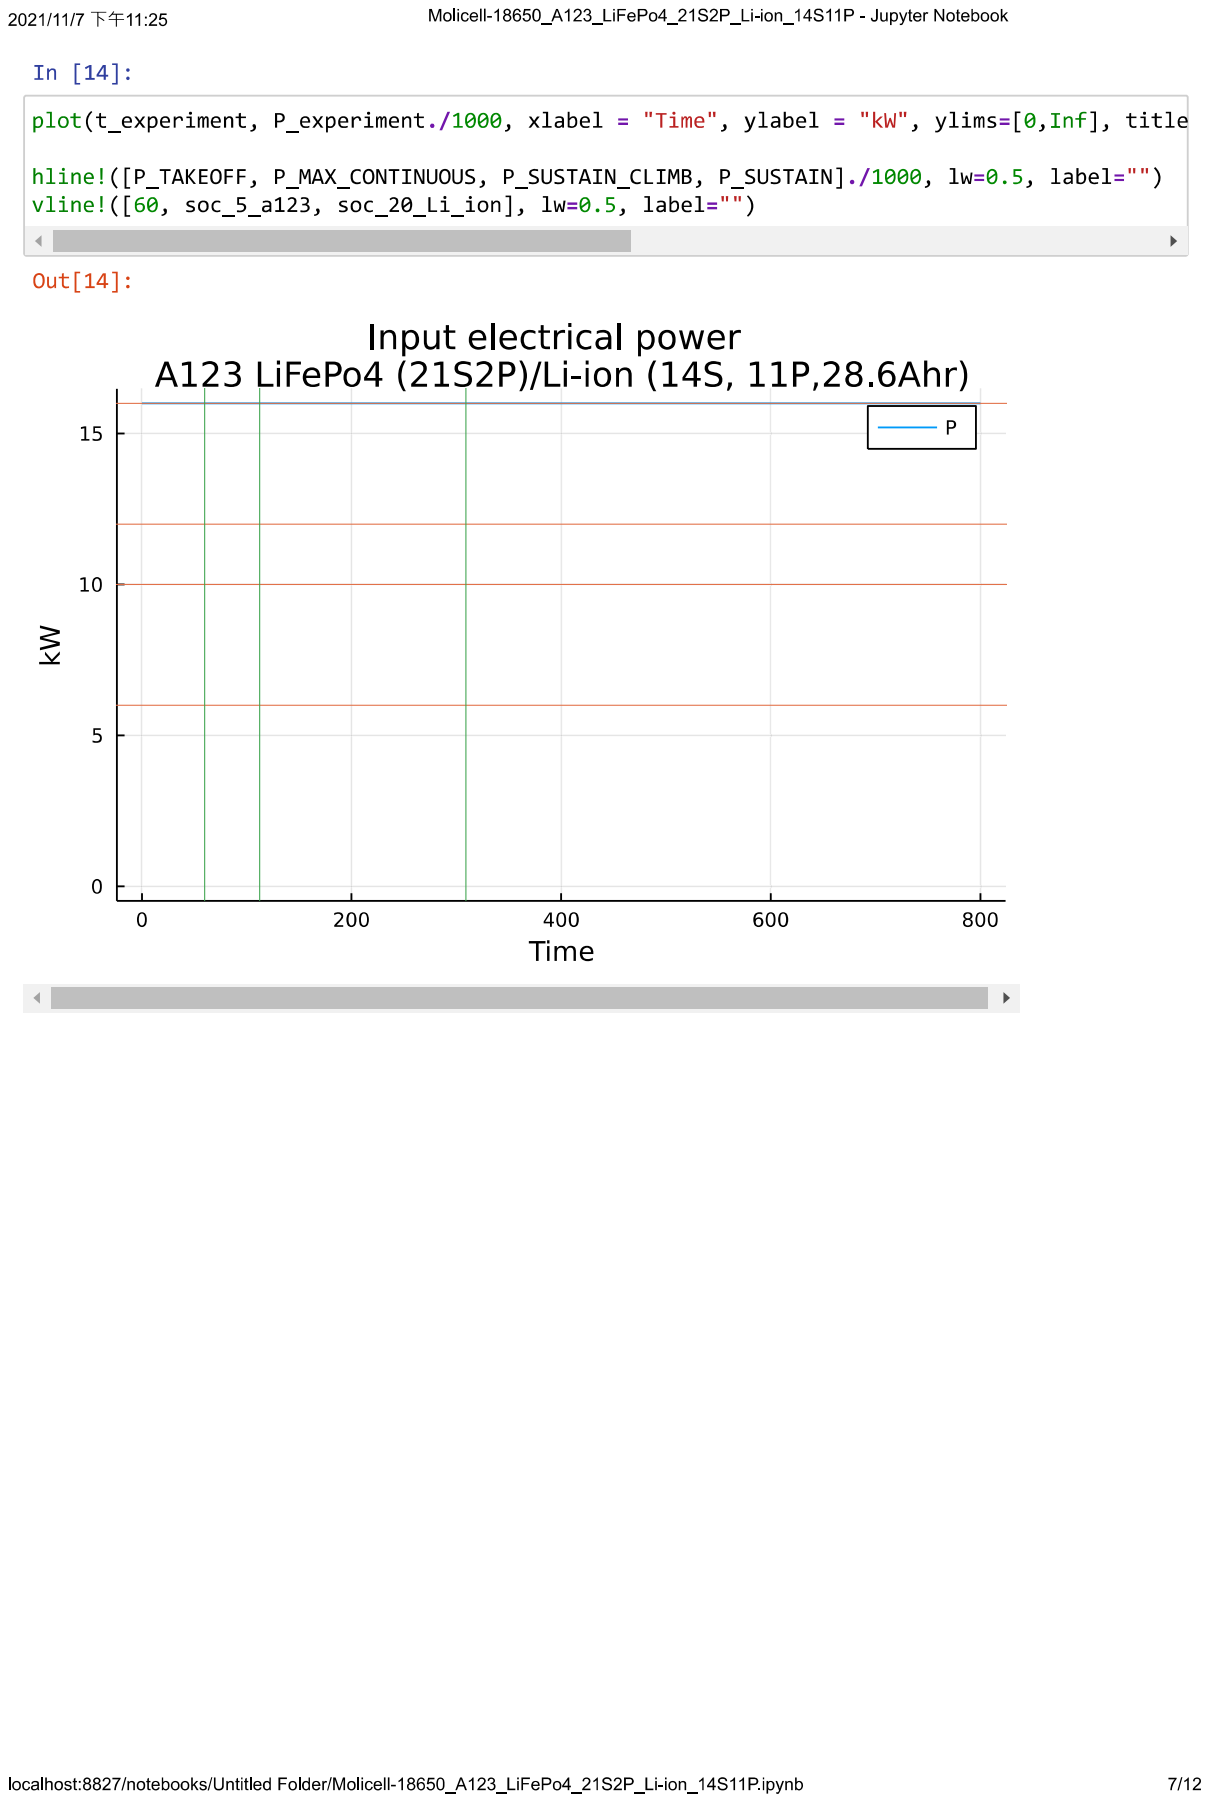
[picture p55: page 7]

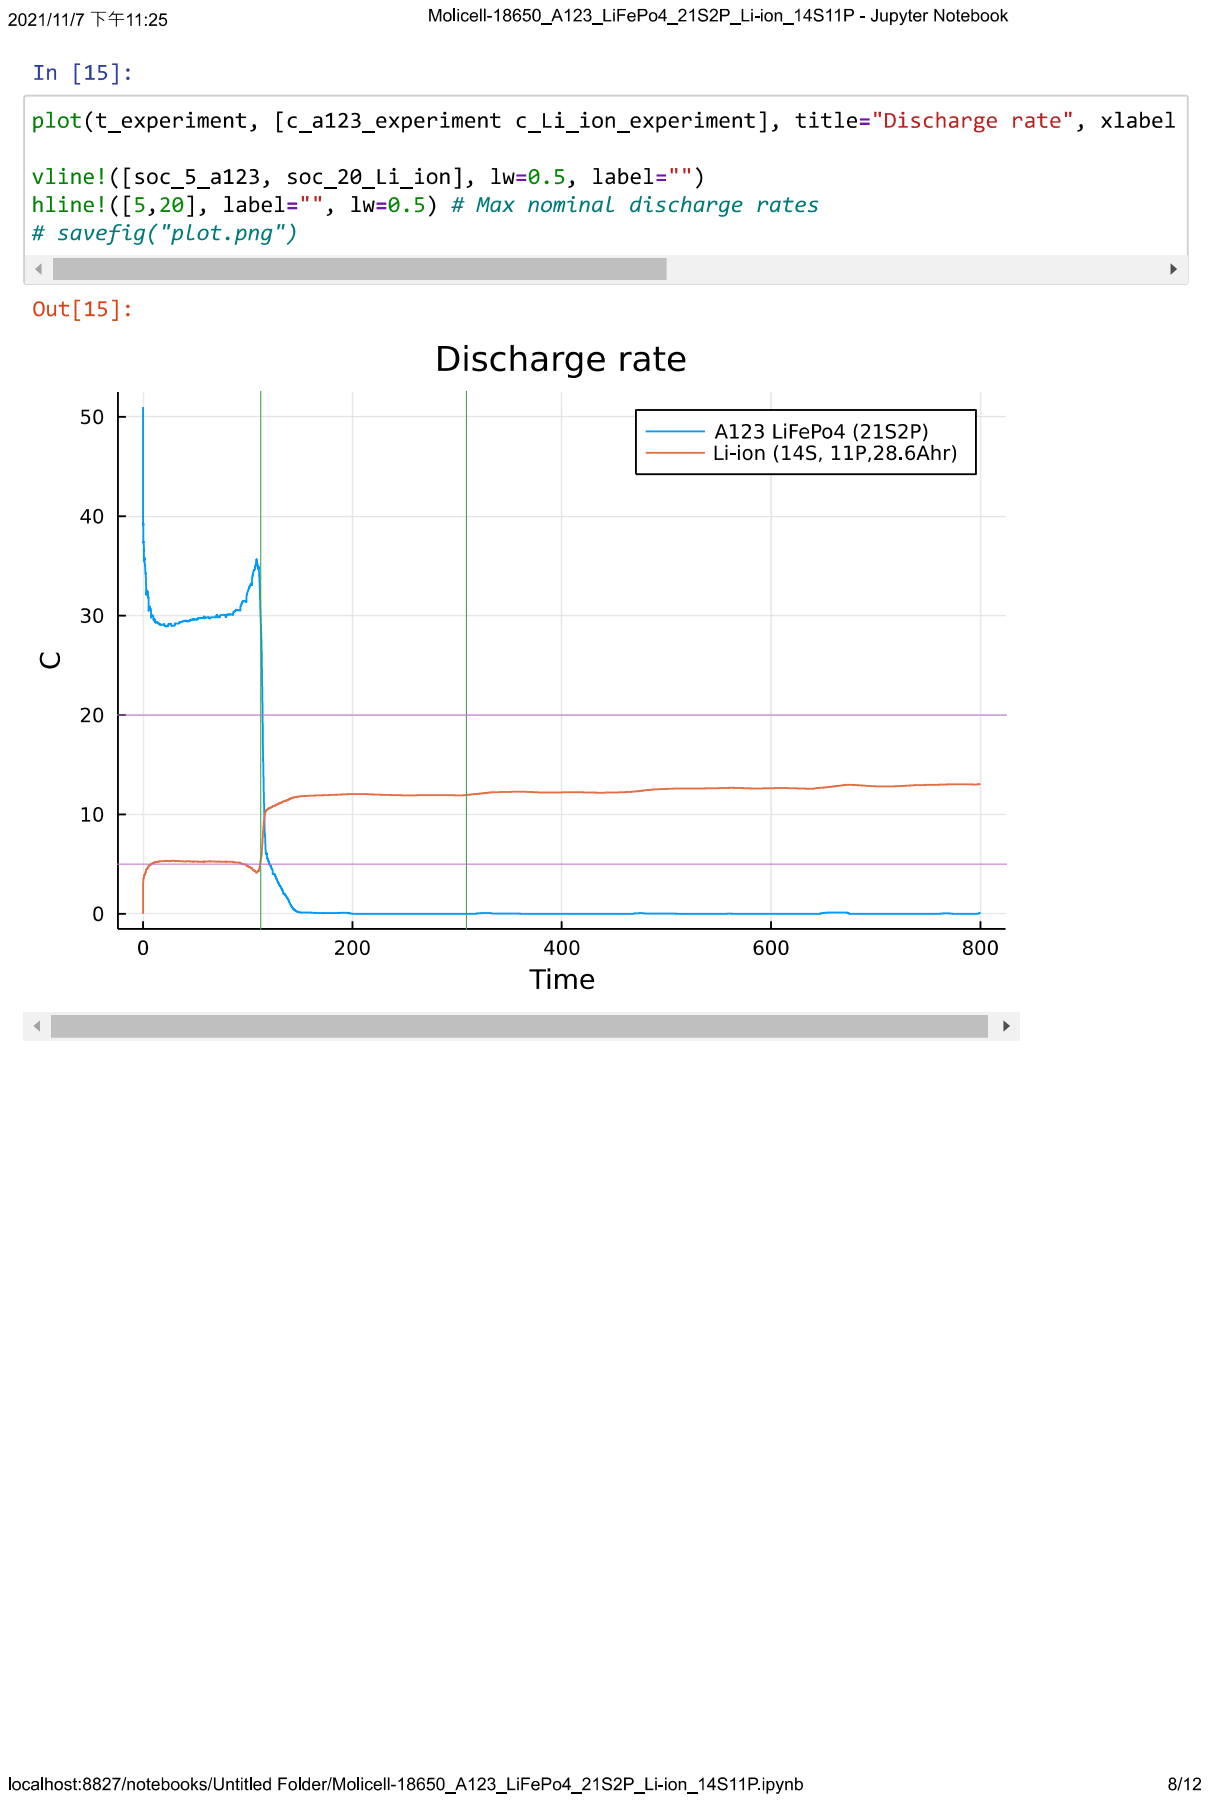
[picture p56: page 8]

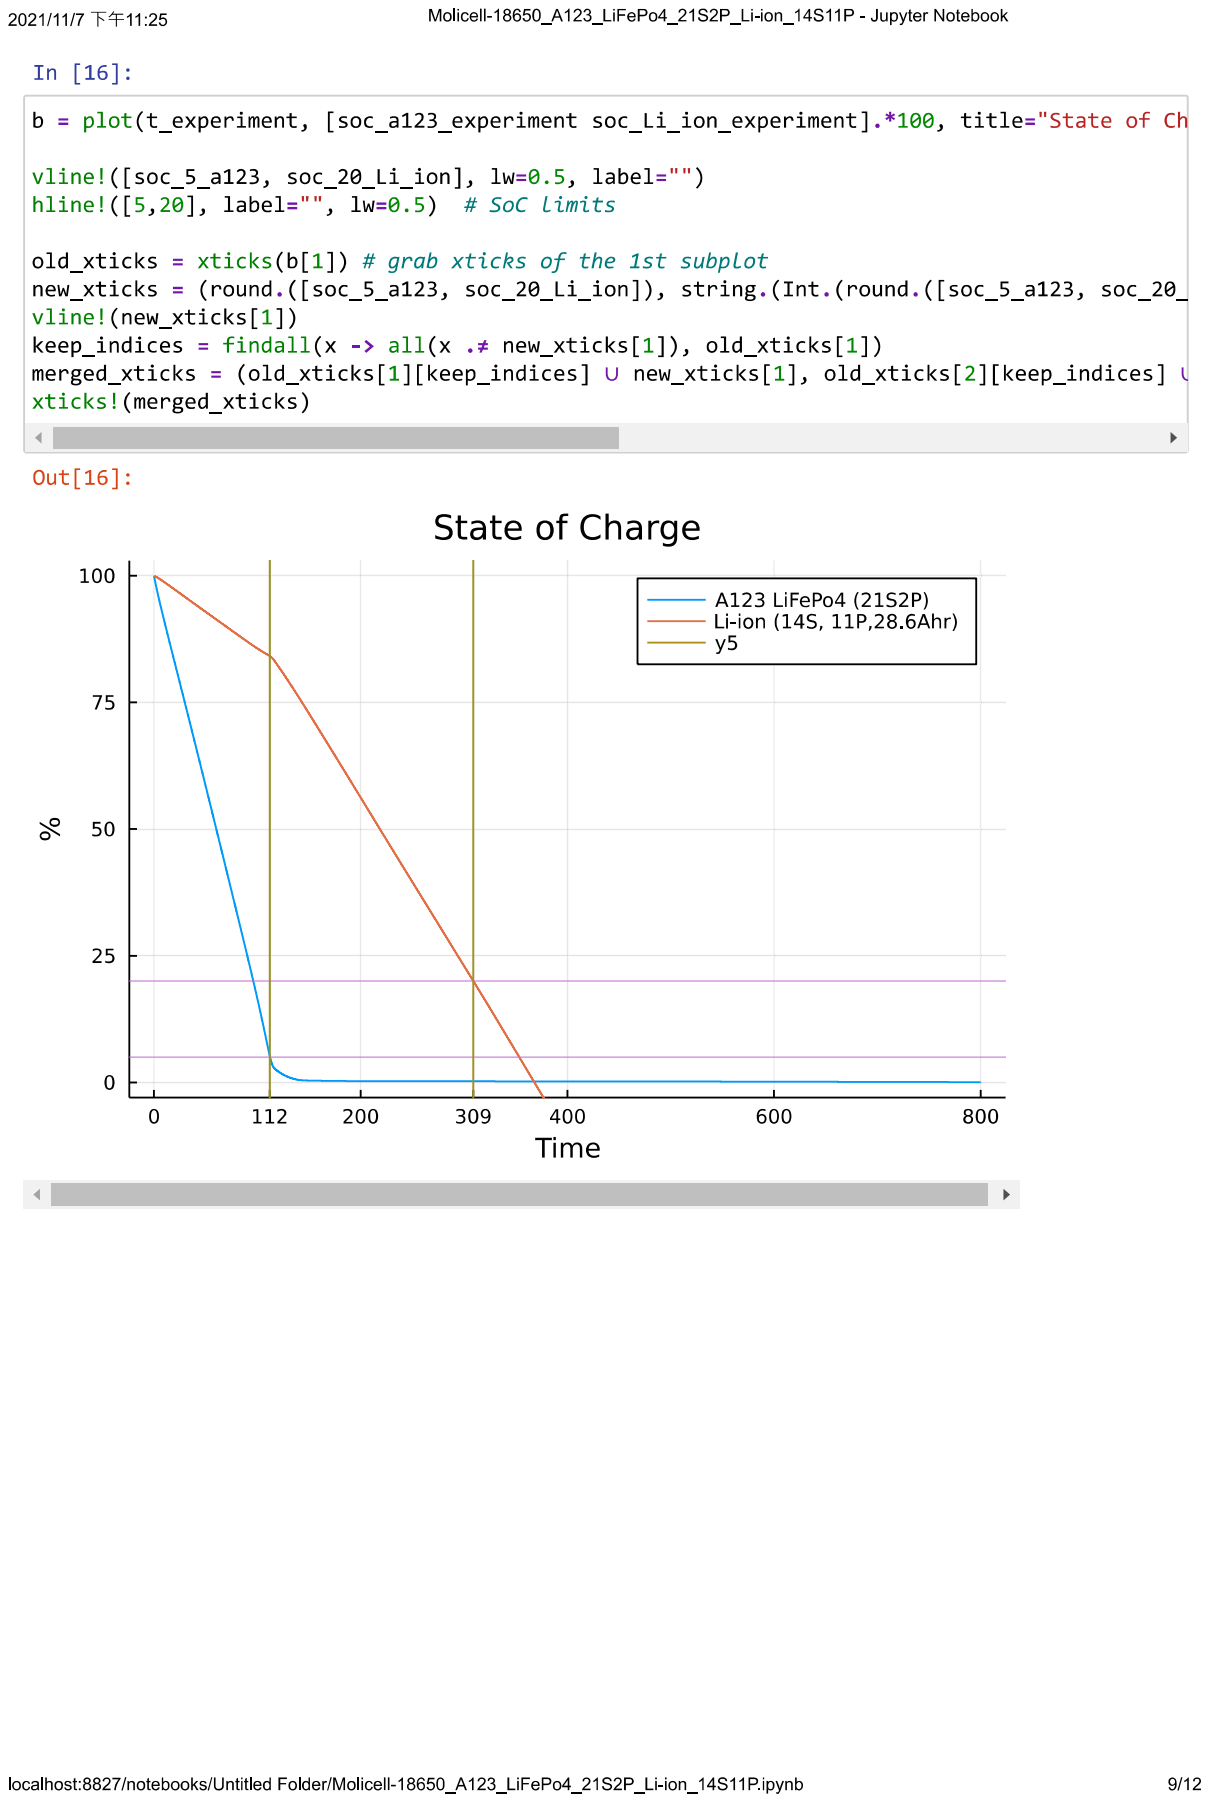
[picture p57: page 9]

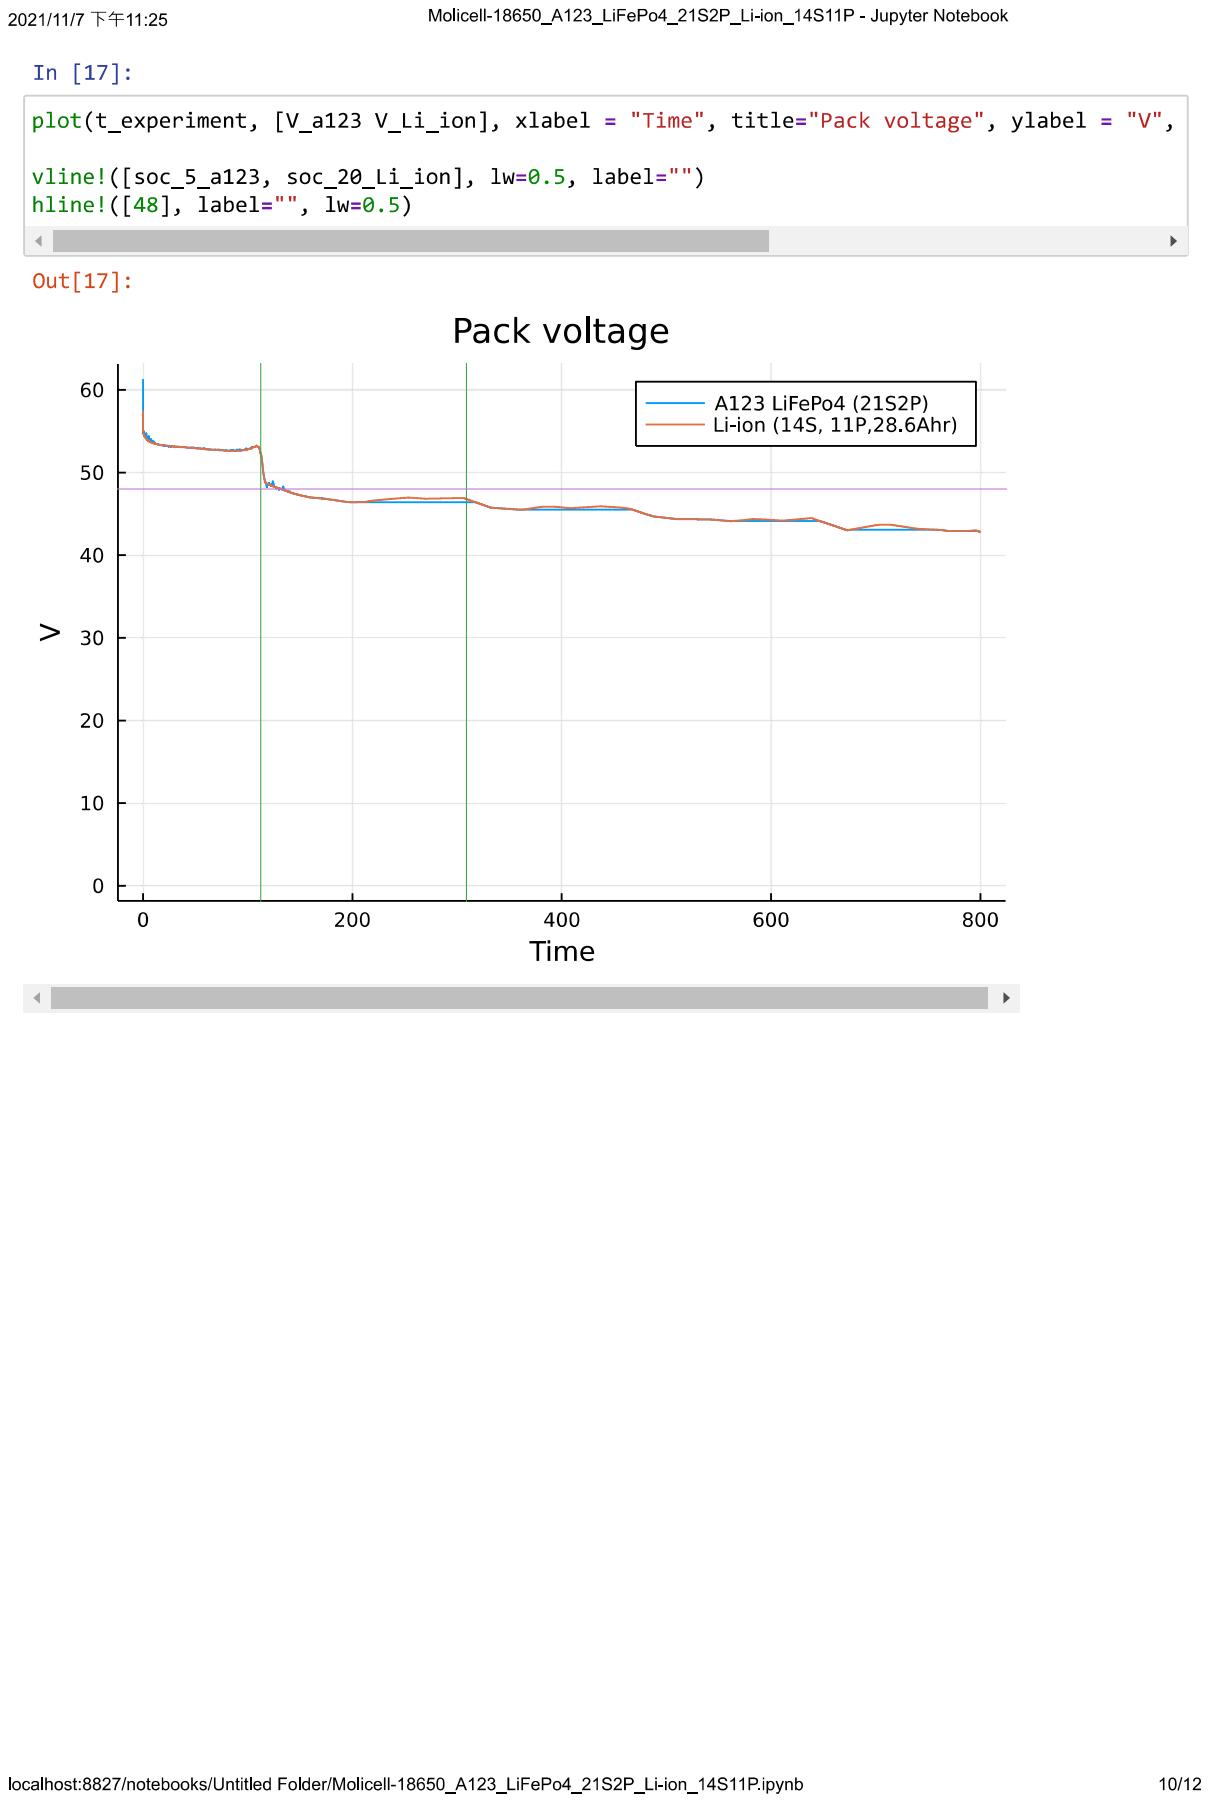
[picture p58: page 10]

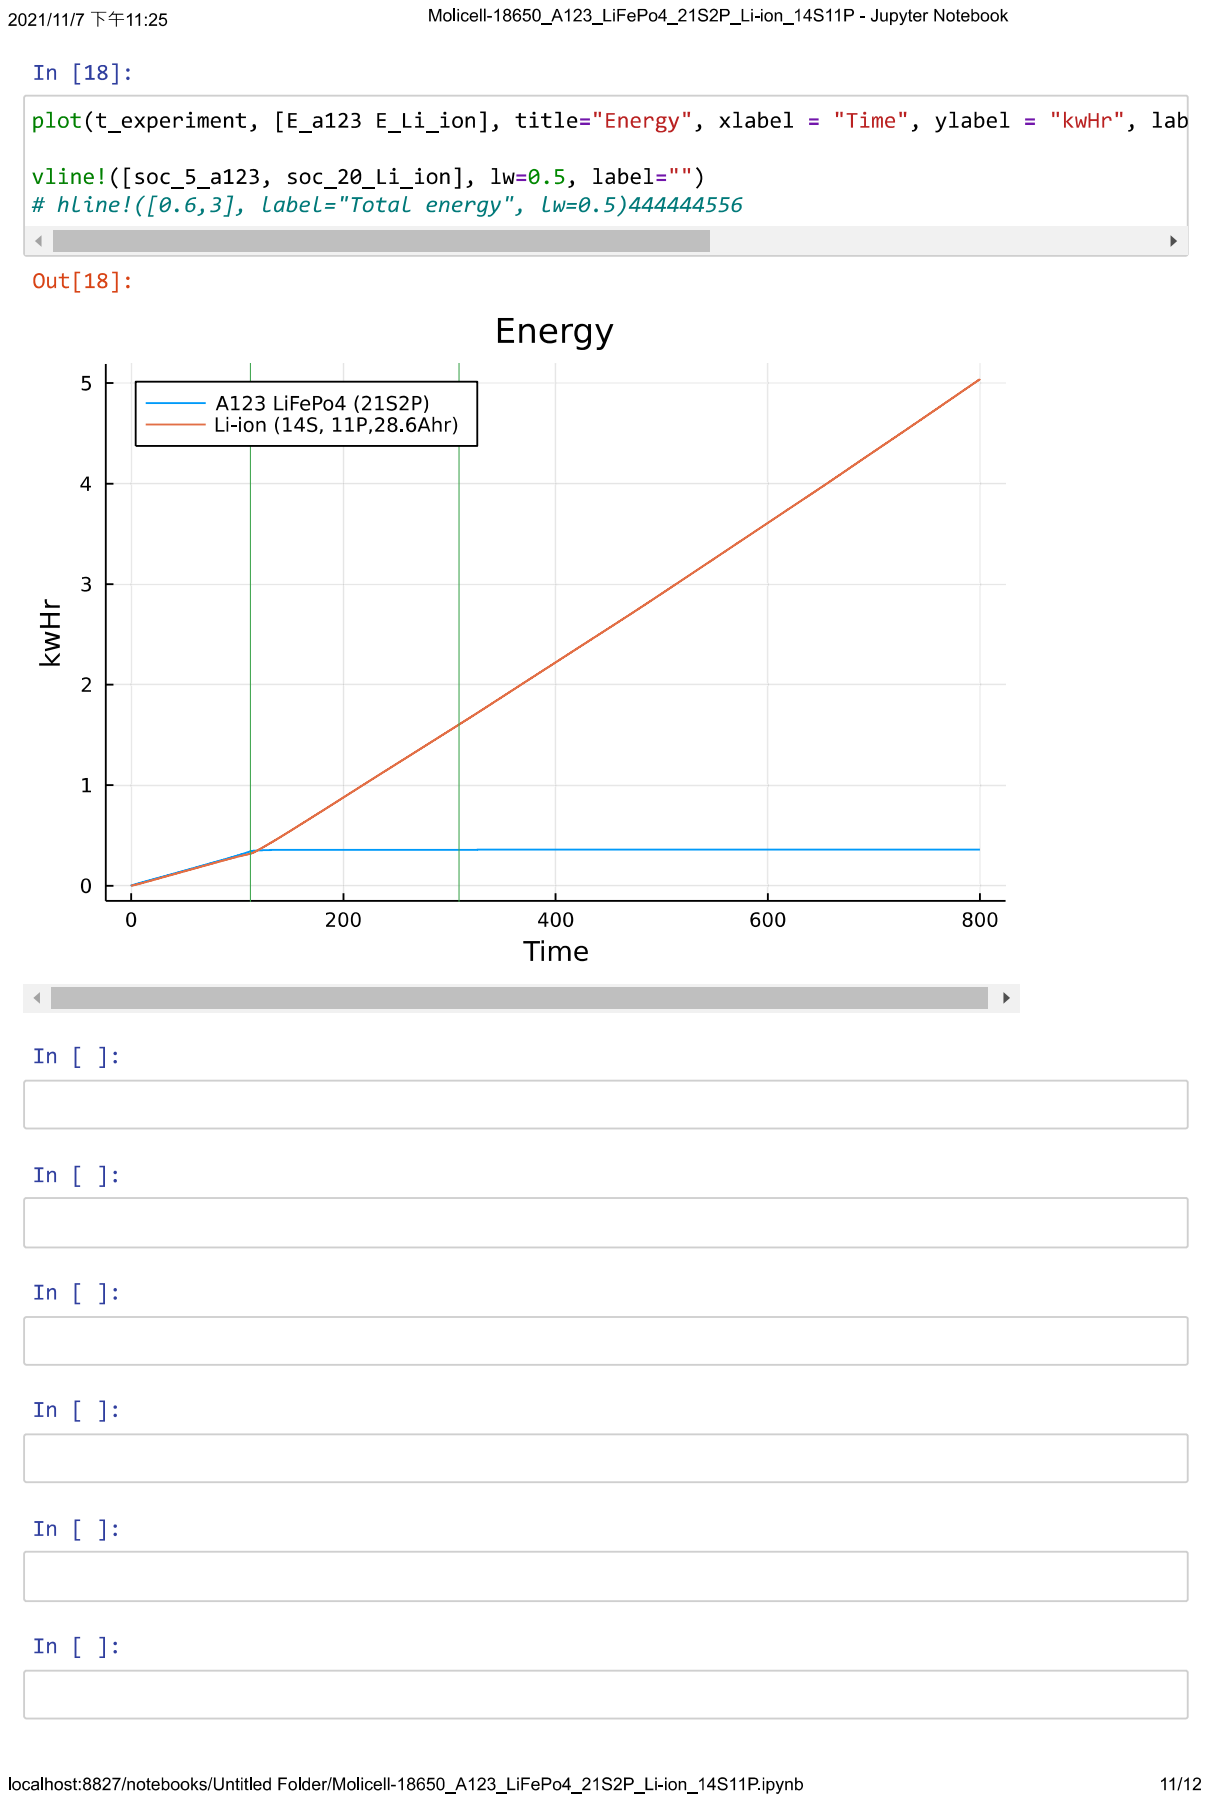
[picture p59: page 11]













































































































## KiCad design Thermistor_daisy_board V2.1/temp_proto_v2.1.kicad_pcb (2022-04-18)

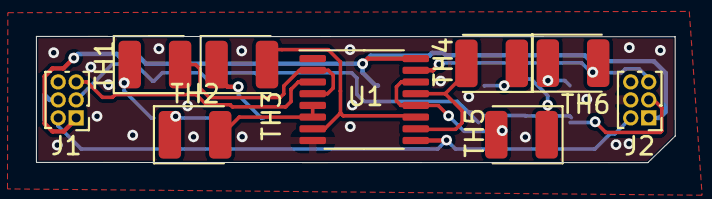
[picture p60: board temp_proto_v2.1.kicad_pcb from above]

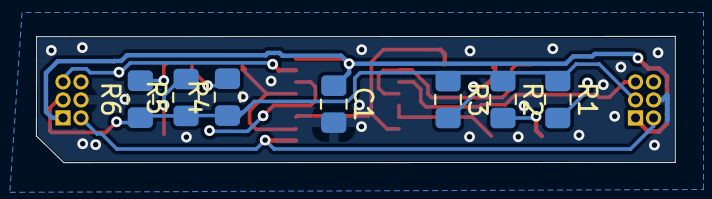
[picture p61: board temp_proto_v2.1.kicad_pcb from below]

Board: 2 copper layers, 35.5 x 7.0 mm, 16 parts (7 on the bottom side), 17 nets.

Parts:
C1: CAP; C_0805_2012Metric_Pad1.15x1.40mm_HandSolder
J1, J2: Conn_02x03_Counter_Clockwise; PinHeader_2x03_P1.00mm_Vertical
R1, R2, R3, R4, R5, R6: R_US; R_0805_2012Metric_Pad1.15x1.40mm_HandSolder
TH1, TH2, TH3, TH4, TH5, TH6: Thermistor_NTC; LED_1210_3225Metric
U1: Hex_d_ff_; TSSOP-16_4.4x5mm_P0.65mm

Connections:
CLK: J1.2, J2.2, U1.9
CONN_1: TH1.2, U1.2, U1.4
CONN_2: TH2.2, U1.5, U1.6
CONN_3: TH3.2, U1.7, U1.11
CONN_4: TH4.2, U1.10, U1.13
CONN_5: TH5.2, U1.12, U1.14
CONN_IN: J1.5, U1.3
CONN_OUT: J2.5, TH6.2, U1.15
GND: C1.2, J1.4, J2.4, U1.8
unnamed: R1.2, TH1.1
unnamed: R2.2, TH2.1
unnamed: R3.2, TH3.1
unnamed: R4.2, TH4.1
unnamed: R5.2, TH5.1
unnamed: R6.2, TH6.1
TEMP_REF: J1.3, J2.3, R1.1, R2.1, R3.1, R4.1, R5.1, R6.1
VCC: C1.1, J1.1, J2.1, U1.16

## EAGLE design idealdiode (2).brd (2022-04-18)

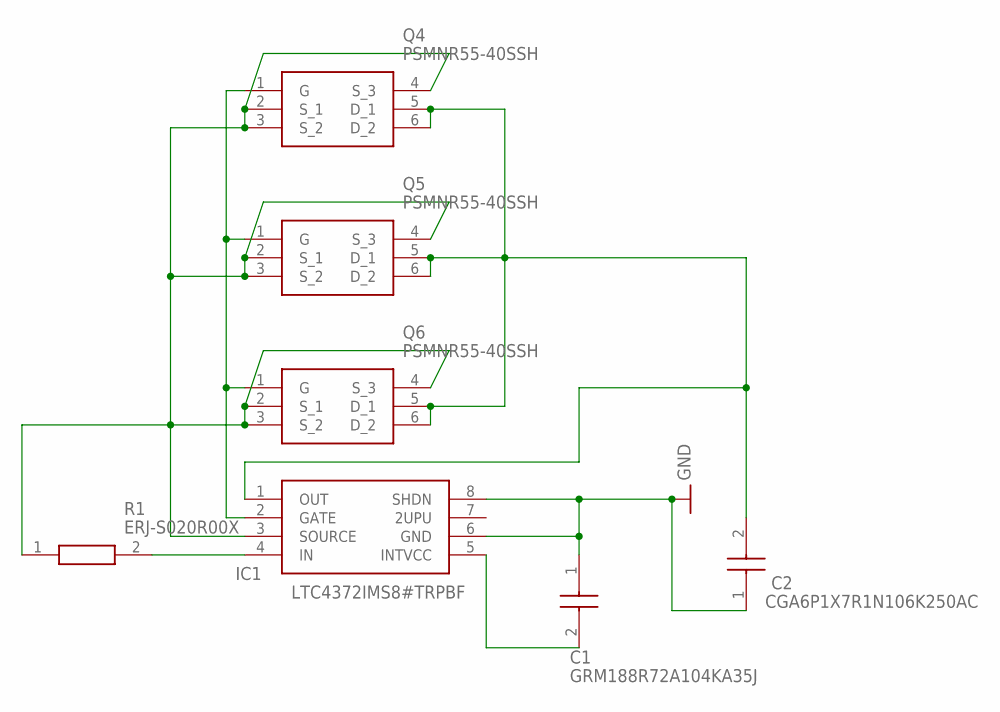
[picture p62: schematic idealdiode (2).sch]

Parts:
C1: GRM188R72A104KA35J; CAPC1608X90N
C2: CGA6P1X7R1N106K250AC; CAPC3225X280N
IC1: LTC4372IMS8#TRPBF; SOP65P490X110-8N
Q4, Q5, Q6: PSMNR55-40SSH; PSMNR5540SSH
R1: ERJ-S020R00X; ERJS02_U02_(0402)

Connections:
GND: C1.1, C2.1, IC1.6 (GND), IC1.8 (SHDN)
unnamed: IC1.2 (GATE), Q4.1 (G), Q5.1 (G), Q6.1 (G)
unnamed: IC1.3 (SOURCE), Q4.2 (S_1), Q4.3 (S_2), Q4.4 (S_3), Q5.2 (S_1), Q5.3 (S_2), Q5.4 (S_3), Q6.2 (S_1), Q6.3 (S_2), Q6.4 (S_3), R1.1
unnamed: C2.2, IC1.1 (OUT), Q4.5 (D_1), Q4.6 (D_2), Q5.5 (D_1), Q5.6 (D_2), Q6.5 (D_1), Q6.6 (D_2)
unnamed: C1.2, IC1.5 (INTVCC)
unnamed: IC1.4 (IN), R1.2

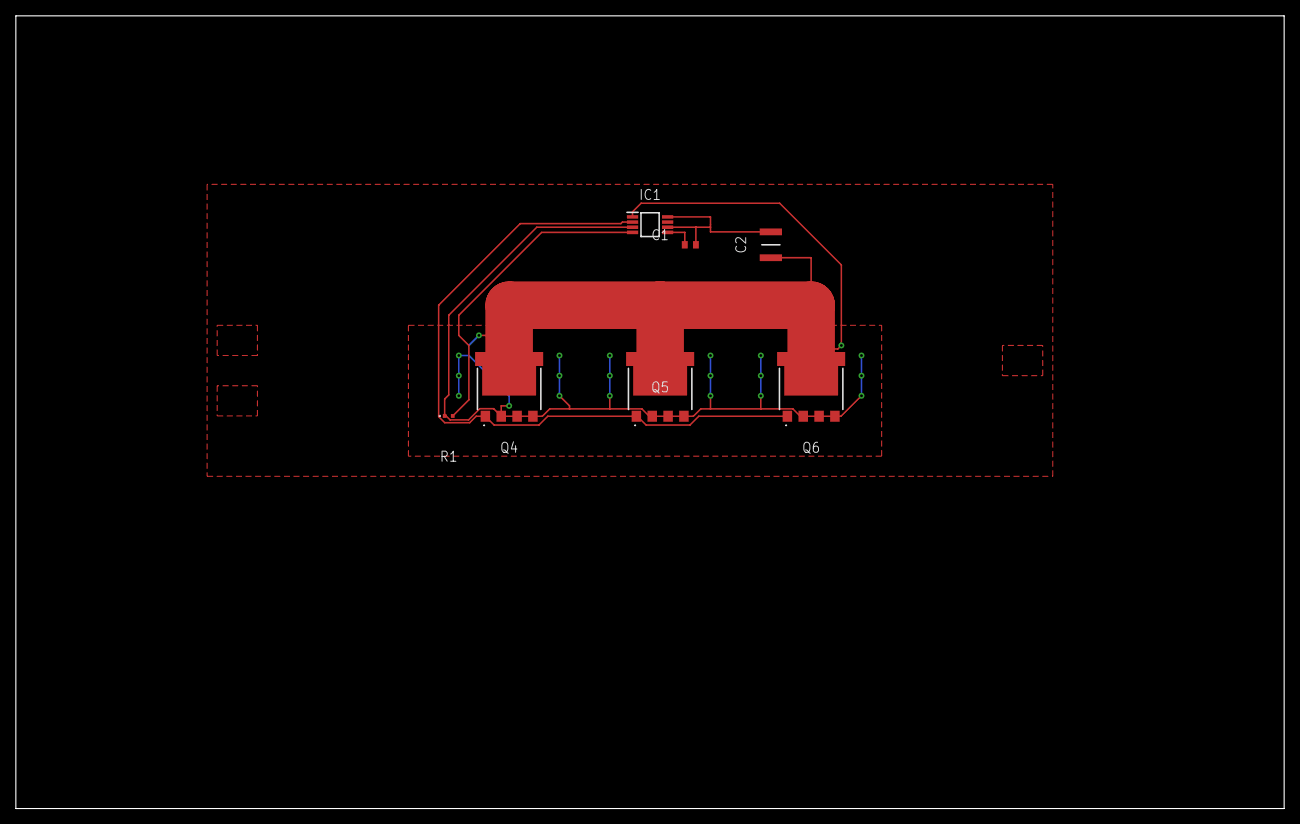
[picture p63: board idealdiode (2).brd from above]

Board: 2 copper layers, 160.0 x 100.0 mm, 7 parts (0 on the bottom side), 6 nets.

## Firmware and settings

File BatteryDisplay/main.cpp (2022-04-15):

/***************************************************************************
**
** Copyright (C) 2017 The Qt Company Ltd.
** Contact: https://www.qt.io/licensing/
**
** This file is part of the examples of the QtBluetooth module of the Qt Toolkit.
**
** $QT_BEGIN_LICENSE:BSD$
** Commercial License Usage
** Licensees holding valid commercial Qt licenses may use this file in
** accordance with the commercial license agreement provided with the
** Software or, alternatively, in accordance with the terms contained in
** a written agreement between you and The Qt Company. For licensing terms
** and conditions see https://www.qt.io/terms-conditions. For further
** information use the contact form at https://www.qt.io/contact-us.
**
** BSD License Usage
** Alternatively, you may use this file under the terms of the BSD license
** as follows:
**
** "Redistribution and use in source and binary forms, with or without
** modification, are permitted provided that the following conditions are
** met:
**   * Redistributions of source code must retain the above copyright
**     notice, this list of conditions and the following disclaimer.
**   * Redistributions in binary form must reproduce the above copyright
**     notice, this list of conditions and the following disclaimer in
**     the documentation and/or other materials provided with the
**     distribution.
**   * Neither the name of The Qt Company Ltd nor the names of its
**     contributors may be used to endorse or promote products derived
**     from this software without specific prior written permission.
**
**
** THIS SOFTWARE IS PROVIDED BY THE COPYRIGHT HOLDERS AND CONTRIBUTORS
** "AS IS" AND ANY EXPRESS OR IMPLIED WARRANTIES, INCLUDING, BUT NOT
** LIMITED TO, THE IMPLIED WARRANTIES OF MERCHANTABILITY AND FITNESS FOR
** A PARTICULAR PURPOSE ARE DISCLAIMED. IN NO EVENT SHALL THE COPYRIGHT
** OWNER OR CONTRIBUTORS BE LIABLE FOR ANY DIRECT, INDIRECT, INCIDENTAL,
** SPECIAL, EXEMPLARY, OR CONSEQUENTIAL DAMAGES (INCLUDING, BUT NOT
** LIMITED TO, PROCUREMENT OF SUBSTITUTE GOODS OR SERVICES; LOSS OF USE,
** DATA, OR PROFITS; OR BUSINESS INTERRUPTION) HOWEVER CAUSED AND ON ANY
** THEORY OF LIABILITY, WHETHER IN CONTRACT, STRICT LIABILITY, OR TORT
** (INCLUDING NEGLIGENCE OR OTHERWISE) ARISING IN ANY WAY OUT OF THE USE
** OF THIS SOFTWARE, EVEN IF ADVISED OF THE POSSIBILITY OF SUCH DAMAGE."
**
** $QT_END_LICENSE$
**
****************************************************************************/

#include <QGuiApplication>
#include <QLoggingCategory>
#include <QQmlApplicationEngine>
#include <QQmlContext>

#include "connectionhandler.h"
#include "devicefinder.h"
#include "devicehandler.h"

#include "heatmapimageprovider.h"

int main(int argc, char *argv[])
{
    // QLoggingCategory::setFilterRules(QStringLiteral("qt.bluetooth* = true"));
    QGuiApplication app(argc, argv);

    ConnectionHandler connectionHandler;
    DeviceHandler deviceHandler;
    DeviceFinder deviceFinder(&deviceHandler);

    qmlRegisterUncreatableType<DeviceHandler>("Shared", 1, 0, "AddressType", "Enum is not a type");

    QQmlApplicationEngine engine;
    engine.rootContext()->setContextProperty("connectionHandler", &connectionHandler);
    engine.rootContext()->setContextProperty("deviceFinder", &deviceFinder);
    engine.rootContext()->setContextProperty("deviceHandler", &deviceHandler);

    engine.addImageProvider("heat_map", new HeatMapImageProvider());

    engine.load(QUrl(QStringLiteral("qrc:/qml/main.qml")));

    return app.exec();

}

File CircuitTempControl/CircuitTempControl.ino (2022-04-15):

//Set I/O
const int INPUT_PIN = A1;
//set pins to variable note: cannnot be const since they will be changed 
int OUTPUT_RELAY = D2;


void setup() {
  // put your setup code here, to run once:
  Serial.begin(115200);
  delay(1000);
  pinMode(INPUT_PIN,INPUT);
  pinMode(OUTPUT_RELAY,OUTPUT);
  //Resolution specific to arduino
  analogReadResolution(12);
}

void loop() {
  // put your main code here, to run repeatedly:
  digitalWrite(OUTPUT_RELAY, LOW);
  int sensorReading = analogRead(INPUT_PIN);
  double voltageTherm = (sensorReading/4095.0) * 3.3;
  double Rs = 10000; 
  double currentBias = (voltageTherm - 3.3) / -Rs; // currentBias is in A; 
  double resistance = (voltageTherm / currentBias); // resistance is in ohms
  double var_temp = log(resistance/11000) + (3977/298.0);
  double temperature = 3977 / var_temp; // finds T in kelvin
  double tempC = temperature - 273.0; //converts T to celsius
  String p1 = ";";
  Serial.print(voltageTherm+p1+tempC);
  Serial.print('\n');
  delay(500); //change to desired sampling rate 
  if (tempC >= 50)// change to desired temperature 
  {
    digitalWrite(OUTPUT_RELAY, HIGH);
    delay(30000); //Change to desired timer(ms) 
    }
}

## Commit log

2022-01-26 Code for temp control
    Using an arduino BLE
2022-01-27 updated some values for base arduino
    1023bit for non ble arduinos - may use megas
2022-04-15 Renders of Thermistor cell boards
    - add grbr/ kicad files
2022-04-15 Create BatteryDisplay
    App for Battery Display
2022-04-15 Add files via upload
    Battery Display App
2022-04-16 Design files for thermistor daisy chain boards
    Done in KiCad verion 6. Full data for print GBR/Drill
2022-04-17 Create battery_testbench_v1.00.lisp
    Automated battery pack testbench using Lisp
2022-04-18 Ideal Diode Controller PCB
    [idealdiode (2).brd, idealdiode (2).sch]
2022-04-18 Thermistor daisy board unzipped
    + read_me
    [temp_proto_v2-B_Cu.gbl, temp_proto_v2-B_Mask.gbs, temp_proto_v2-B_Paste.gbp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]
2022-04-27 Updated heatmapimageprovider.cpp
    add additional json array variable and how the data will draw uonto the map
2022-04-29 Add files via upload
    naive testbench for motor current control
2022-04-29 Delete Directory
    File names contain spaces, causing failiure to pull needs to be re named
    [0.2C.xlsx, 100W.xlsx, 20A.xlsx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]
2022-04-29 Delete 3D_Battery_holders directory
    pull issue
    [Soporte_baterías_26650x10_base_inferior.stl, Soporte_baterías_26650x10_base_superior.stl, Soporte_tapa_derecha.stl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]
2022-04-30 Delete Prototype_Test directory
    Directory has space " prototype_test(space)" error pulling
